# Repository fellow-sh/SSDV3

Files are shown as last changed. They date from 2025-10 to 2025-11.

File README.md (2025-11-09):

<p style="text-align: center;font-weight: bold;">This project has been migrated to the UBCO Aerospace Club <a href="https://github.com/UBCOAerospaceClub/2025_SSDV3">2025_SSDV3</a> fork.</p>

# The Super Step Down V3

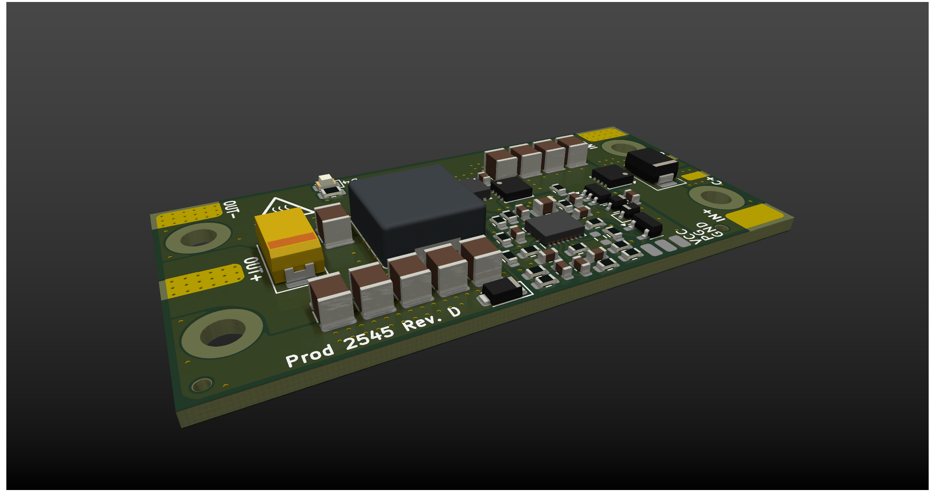
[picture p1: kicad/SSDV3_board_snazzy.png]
Top View


The SSDV3 is an independently-made, non-isolated DC/DC converter designed for unmanned aerial systems (UAS). The module is intended for converting 50V battery input down to 5-12V output at a maximum load of 8A. It acts as a reliable battery-eliminator circuit (BEC) through effective regulation in the presence of voltage transients caused by high-power brushless motors.

## Specifications

<table><tbody>
  <tr>
    <td>Input Voltage</td>
    <td>20-60V</td>
  </tr>
  <tr>
    <td>Max Transient Voltage</td>
    <td>100V (clamping starts at 70V)</td>
  </tr>
  <tr>
    <td>Output Voltage(s)</td>
    <td>5.1V, 7.4V, 9.6V, 12V</td>
  </tr>
  <tr>
    <td>Thermal Max Output Current</td>
    <td>5A</td>
  </tr>
  <tr>
    <td>Designed Max Output Current</td>
    <td>8A</td>
  </tr>
  <tr>
    <td>Lowest Typical Efficiency</td>
    <td>89%</td>
  </tr>
  <tr>
    <td>Est. Voltage Overshoot</td>
    <td>200mV</td>
  </tr>
</tbody>
</table>

*Specifications are from design, not tested.*

## Comparison with Last Super Step Down

This design is motivated by the challenges encountered by the [UBCO Aerospace Club](https://github.com/UBCOAerospaceClub) with their Jellyfish quadcopter when powering auxiliary electronics off the drone's main battery. Lessons were learned through a variety of integration failures, investigations, and validation testing, and these experiences informed the development of version 3 of the Super Step Down series.

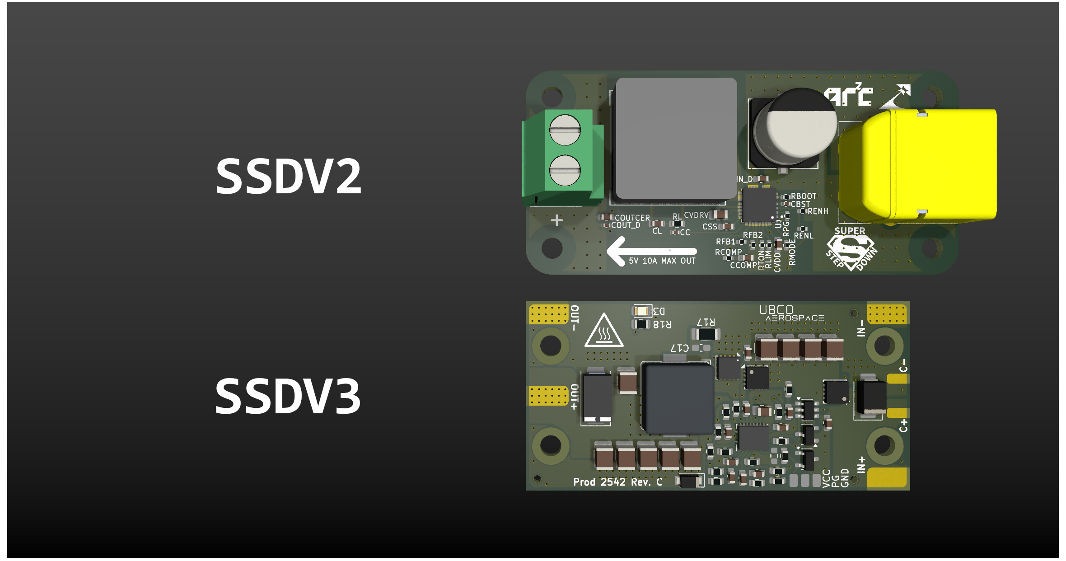
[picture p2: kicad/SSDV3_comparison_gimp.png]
Comparison


**Improvements from the previous version:**

- Dramatically improved regulation during line transients
- Considerable footprint area reduction by 16.5%
- Configurable output voltages instead of a fixed 5V output
- Added ESD protection on inputs
- Reverse polarity protection for the majority of the circuit
- Lower losses by using direct wire solder pads instead of terminal block

## Copyright Notice

Copyright &#169; Julian Joaquin 2025

Hardware Source Licensed under CERN-OHL-W version 2

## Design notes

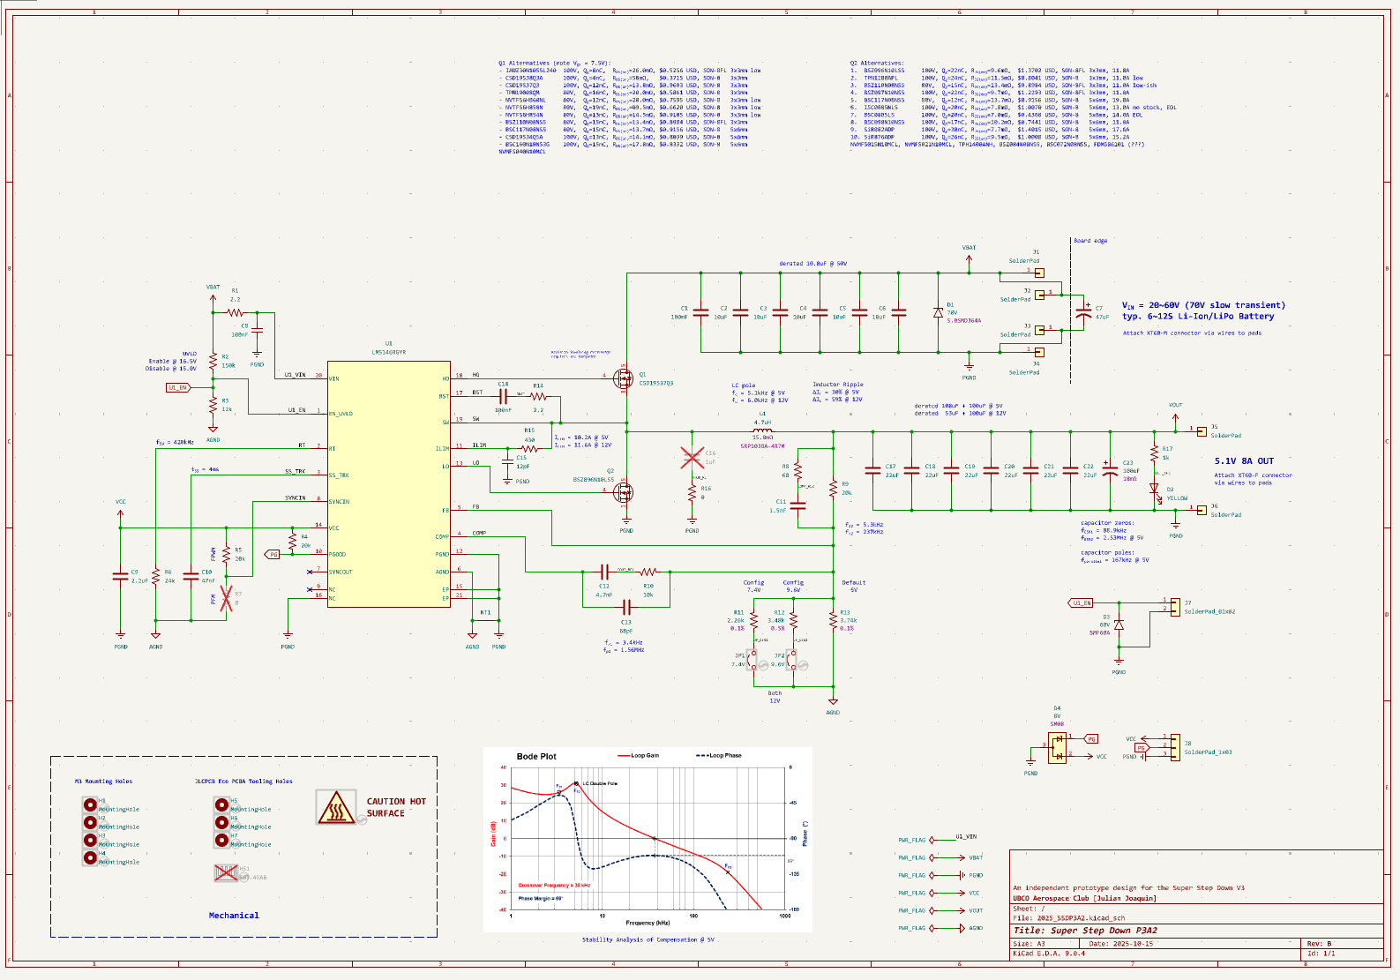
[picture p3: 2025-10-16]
kicad/SSDV3_schematic.png

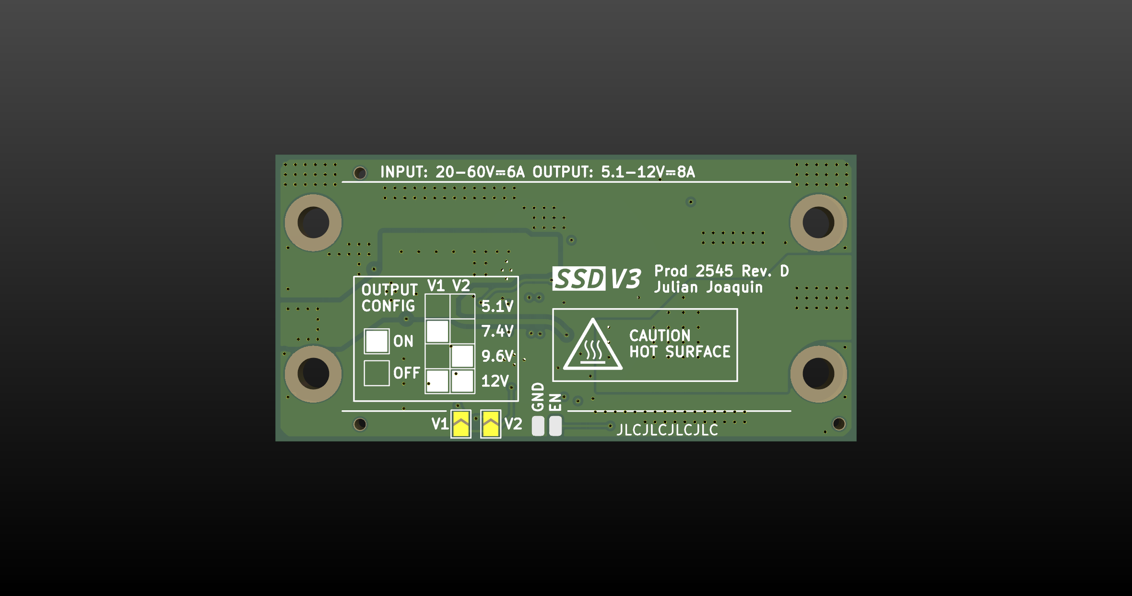
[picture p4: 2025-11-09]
kicad/SSDV3_board_bottom.png

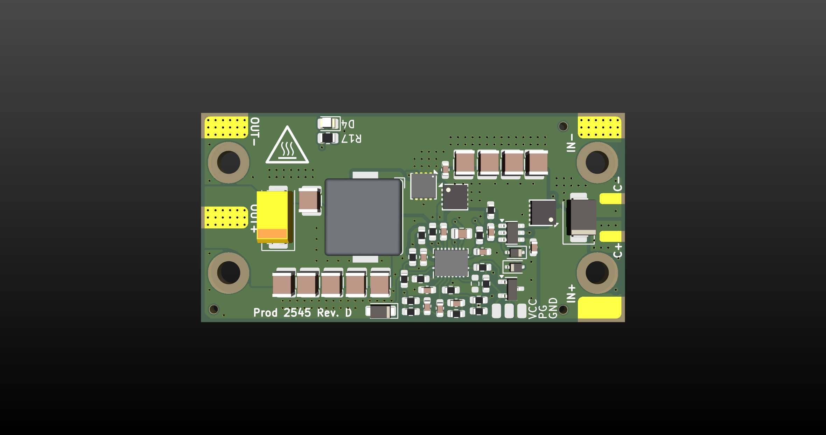
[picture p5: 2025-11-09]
kicad/SSDV3_board_top.png

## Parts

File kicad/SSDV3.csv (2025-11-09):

Value | Reference | Footprint | Datasheet | Part Number | Description | LCSC PN | Part Type | Manufacturer
2.2uF | C10 | Capacitor_SMD:C_0805_2012Metric | ~ | GRM21BR71E225KE11L | CAP CER 2.2uF 25V X7R 10% 0805 | C77081 | Extended | Murata Electronics
47nF | C11 | Capacitor_SMD:C_0603_1608Metric | ~ | CL10B473KB8NNNC | CAP CER 47nF 50V X7R 10% 0603 | C1622 | Basic | Panasonic
1.5nF | C12 | Capacitor_SMD:C_0603_1608Metric | ~ | 0603B152K500NT | CAP CER 1.5nF 50V X7R 10% 0603 | C1595 | Preferred Extended | Guangdong Fenghua
4.7nF | C13 | Capacitor_SMD:C_0603_1608Metric | ~ | 0603B472K500NT | CAP CER 4.7nF 50V X7R 10% 0603 | C53987 | Basic | Guangdong Fenghua
68pF | C14 | Capacitor_SMD:C_0603_1608Metric | ~ | CL10C680JB8NNNC | CAP CER 68pF 50V C0G 5% 0603 | C28262 | Preferred Extended | Panasonic
12pF | C16 | Capacitor_SMD:C_0603_1608Metric | ~ | CC0603JRNPO0BN120 | CAP CER 12pF 100V NP0 5% 0603 | C576801 | Extended | YAGEO
100uF | C23 | Capacitor_Tantalum_SMD:CP_EIA-7343-20_Kemet-V_HandSolder | https://search.kemet.com/download/specsheet/T521D107M025ATE040 | T521D107M025ATE040 | CAP TANT 100uF 25V 20% 7343 | C696814 | Extended | KEMET
22uF | C17,C18,C19,C20,C21,C22 | Capacitor_SMD:C_1210_3225Metric | https://product.samsungsem.com/mlcc/CL32B226KAJNNN.do | CL32B226KAJNNNE | CAP CER 22uF 25V X7R 10% 1210 | C309062 | Extended | Panasonic
100nF | C2,C3,C4,C9,C15 | Capacitor_SMD:C_0603_1608Metric | https://www.yageogroup.com/products/Capacitors/part/CC0603KRX7R0BB104 | CC0603KRX7R0BB104 | CAP CER 100nF 100V X7R 10% 0603 | C113803 | Extended | YAGEO
10uF | C5,C6,C7,C8 | Capacitor_SMD:C_1210_3225Metric | ~ | GRM32EC72A106KE05L | CAP CER 10uF 100V X7S 10% 1210 | C576517 | Extended | Murata Electronics
64V | D1 | Diode_SMD:D_SMB | https://jlcpcb.com/api/file/downloadByFileSystemAccessId/8564879160893476864 | SMBJ64CA | DIODE TVS 64V 600W BI SMB | C41376099 | Preferred Extended | Zhuhai Hongjiacheng
GREEN | D4 | LED_SMD:LED_0805_2012Metric | ~ | KT-0805G | LED GREEN 0805 | C2297 | Basic | Hubei KENTO Electronics
60V | D5 | Diode_SMD:D_SMF | https://jlcpcb.com/api/file/downloadByFileSystemAccessId/8564881124892696576 | SMF60CA | DIODE TVS 60V BI SOD-123FL | C41376092 | Preferred Extended | Zhuhai Hongjiacheng
8V | D6 | Package_TO_SOT_SMD:SOT-23-3 | https://jlcpcb.com/api/file/downloadByFileSystemAccessId/8604441956051673088 | SM08 | DIODE TVS DUAL 8V UNI SOT-23 | C42413902 | Preferred Extended | Zhuhai Hongjiacheng
BAT46WS | D2,D3 | Diode_SMD:D_SOD-323 | ~ | BAT46WS | DIODE SCHOTTKY 100V SOD-323 | C7502692 | Preferred Extended | Zhuhai Hongjiacheng
4.7uH | L1 | Inductor_SMD:L_Bourns_SRP1038C_10.0x10.0mm | https://www.bourns.com/docs/Product-Datasheets/SRP1038A.pdf | SRP1038A-4R7M | INDUCTOR 4.7uH 10A 15mΩ | C2041319 | Extended | Bourns
BSZ096N10LS5 | Q3 | Package_SON_JJ:Infineon_PG-TSDSON-8-26_3.3x3.3mm_P0.65mm | https://www.infineon.com/part/BSZ096N10LS5 | BSZ096N10LS5 | MOSFET N-CH 100V 62A TSDSON-8FL | C534695 | Extended | Infineon Technologies
CSD19537Q3 | Q1,Q2 | Package_SON_JJ:Texas_DQG0008A_3.3x3.3mm_P0.65mm_ThermalVias-D0.3mm | http://www.ti.com/lit/ds/symlink/csd19537q3.pdf | CSD19537Q3T | MOSFET N-CH 100V 53A VSON-8(3.3x3.3) | C134143 | Extended | Texas Instruments
150k | R3 | Resistor_SMD:R_0603_1608Metric | ~ | 0603WAF1503T5E | RES 150kΩ 1% 75V 100mW 0603 | C22807 | Basic | UNI-ROYAL
12k | R4 | Resistor_SMD:R_0603_1608Metric | ~ | 0603WAF1202T5E | RES 12kΩ 1% 75V 100mW 0603 | C22790 | Basic | UNI-ROYAL
24k | R7 | Resistor_SMD:R_0603_1608Metric | ~ | 0603WAF2402T5E | RES 24kΩ 1% 75V 100mW 0603 | C23352 | Basic | UNI-ROYAL
10k | R11 | Resistor_SMD:R_0603_1608Metric | ~ | 0603WAF1002T5E | RES 10kΩ 1% 75V 100mW 0603 | C25804 | Basic | UNI-ROYAL
6.81k | R12 | Resistor_SMD:R_0603_1608Metric | ~ | RT0603BRD076K81L | RES 6.81kΩ 0.1% 50V 100mW 0603 | C861538 | Extended | YAGEO
3.48k | R13 | Resistor_SMD:R_0603_1608Metric | ~ | 0603WAD3481T5E | RES 3.48kΩ 0.5% 50V 100mW 0603 | C423043 | Extended | UNI-ROYAL
3.74k | R14 | Resistor_SMD:R_0603_1608Metric | https://www.yageogroup.com/products/Resistors/part/RT0603BRE073K74L | RT0603BRE073K74L | RES 3.74kΩ 0.1% 75V 100mW 0603 | C849741 | Extended | YAGEO
430 | R16 | Resistor_SMD:R_0603_1608Metric | ~ | 0603WAF4300T5E | RES 430Ω 1% 75V 100mW 0603 | C23170 | Preferred Extended | UNI-ROYAL
1k | R17 | Resistor_SMD:R_0805_2012Metric | ~ | 0805W8F1001T5E | RES 1kΩ 1% 150V 125mW 0805 | C17513 | Basic | UNI-ROYAL
68 | R1,R9 | Resistor_SMD:R_0603_1608Metric | ~ | 0603WAF680JT5E | RES 68Ω 1% 75V 100mW 0603 | C27592 | Preferred Extended | UNI-ROYAL
2.2 | R2,R15 | Resistor_SMD:R_0603_1608Metric | ~ | 0603WAF220KT5E | RES 2.2Ω 1% 75V 100mW 0603 | C22939 | Basic | UNI-ROYAL
20k | R5,R6,R10 | Resistor_SMD:R_0603_1608Metric | ~ | 0603WAF2002T5E | RES 20kΩ 1% 75V 100mW 0603 | C4184 | Basic | UNI-ROYAL
LM5050-1 | U1 | Package_TO_SOT_SMD:TSOT-23-6 | http://www.ti.com/lit/ds/symlink/lm5050-1-q1.pdf | LM5050-1 | IC HIGH SIDE FET controller TSOT-23-6 | C473393 | Extended | Texas Instruments
LM5146 | U2 | Package_QFN_JJ:Texas_RGY0020B_EP_3.5x4.5mm_P0.5mm_ThermalVias-D0.3mm | https://www.ti.com/lit/gpn/lm5146 | LM5146RGYR | IC BUCK SYNC Controller VQFN-20 | C3188679 | Extended | Texas Instruments

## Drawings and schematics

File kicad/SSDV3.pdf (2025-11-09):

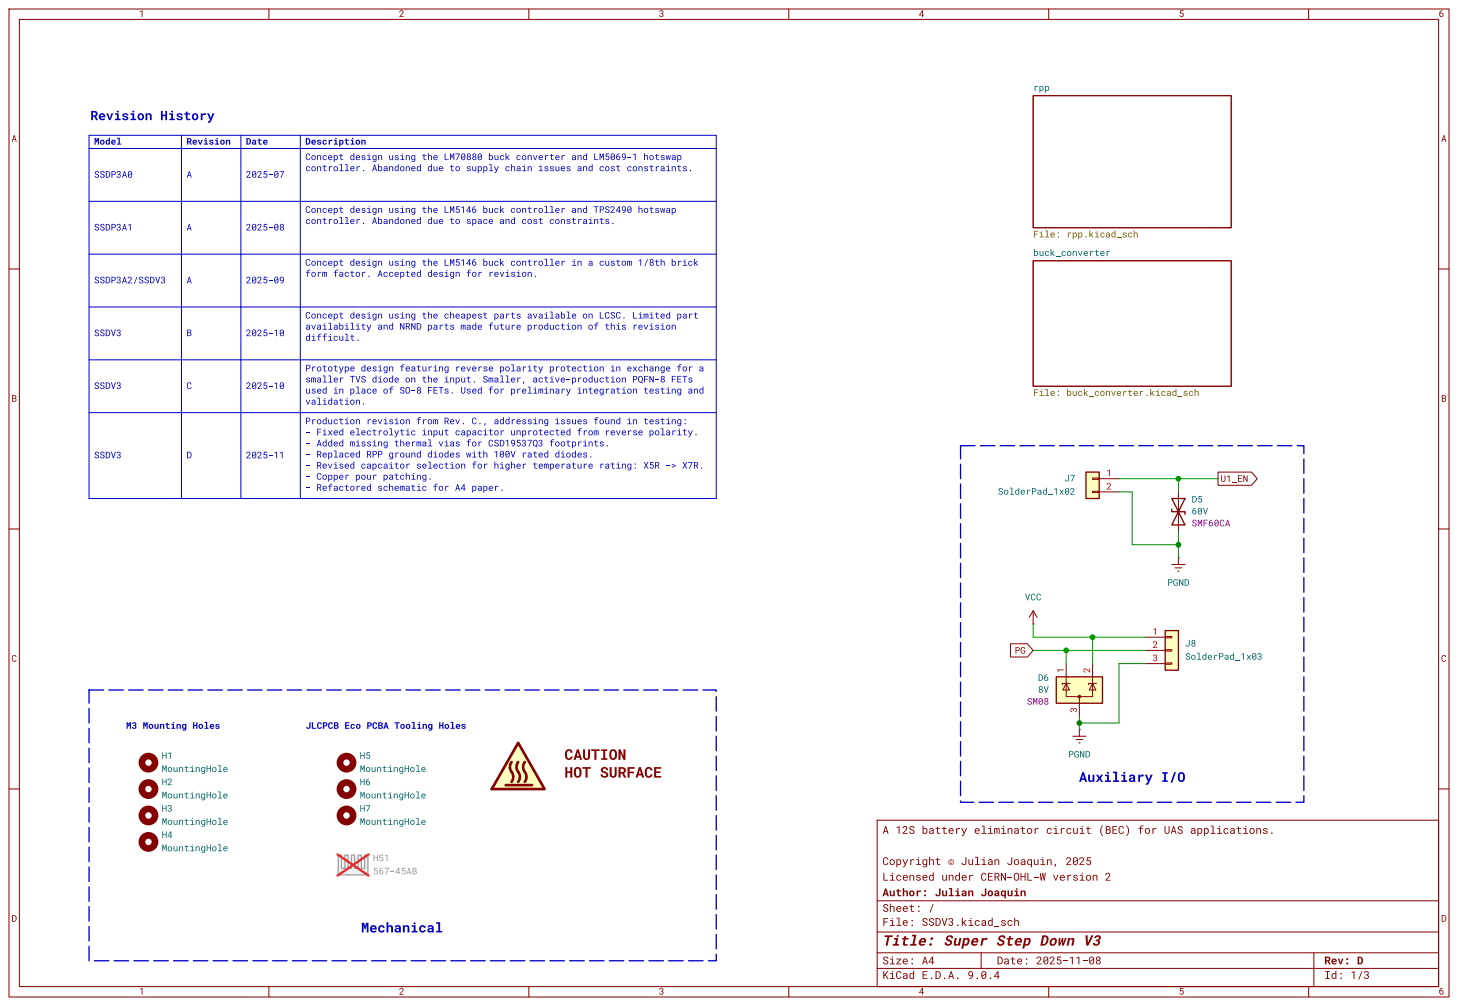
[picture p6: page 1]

Revision A C | Date 2025-07 2025-10 | Description SSDP3A0 Concept design using the LM70880 buck converter and LM5069-1 hotswap difficult. SSDV3 Prototype design featuring reverse polarity protection in exchange for a | PG Model

A | 2025-08 | controller. Concept design using the LM5146 buck controller Abandoned due to supply chain issues and cost constraints. SSDP3A1 and TPS2490 hotswap

A | 2025-09 | controller. Concept design using the LM5146 buck controller Abandoned due to space and cost constraints. SSDP3A2/SSDV3 in a custom 1/8th brick

B | 2025-10 | form factor. Concept design using the cheapest parts available Accepted design for revision. SSDV3 and NRNDparts made future production on LCSC. Limited of this revision part availability

smaller TVS diode on the input. Smaller, active-production integration PQFN-8 FETs used in place of SO-8 FETs. Used for preliminary testing and

JLCPCB Eco PCBA Tooling Holes

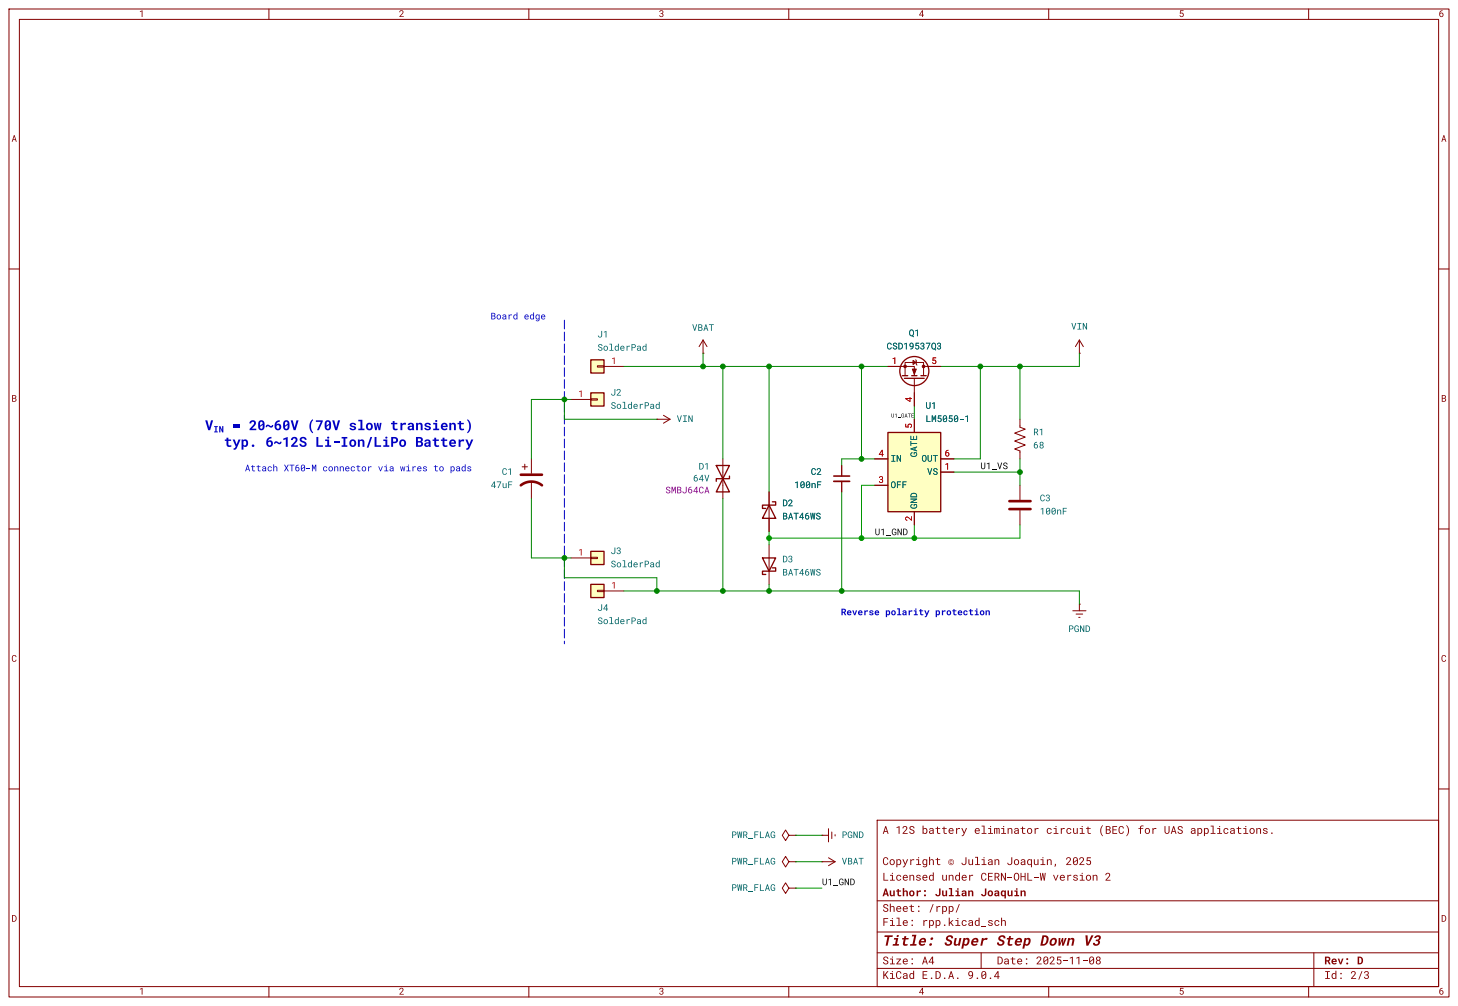
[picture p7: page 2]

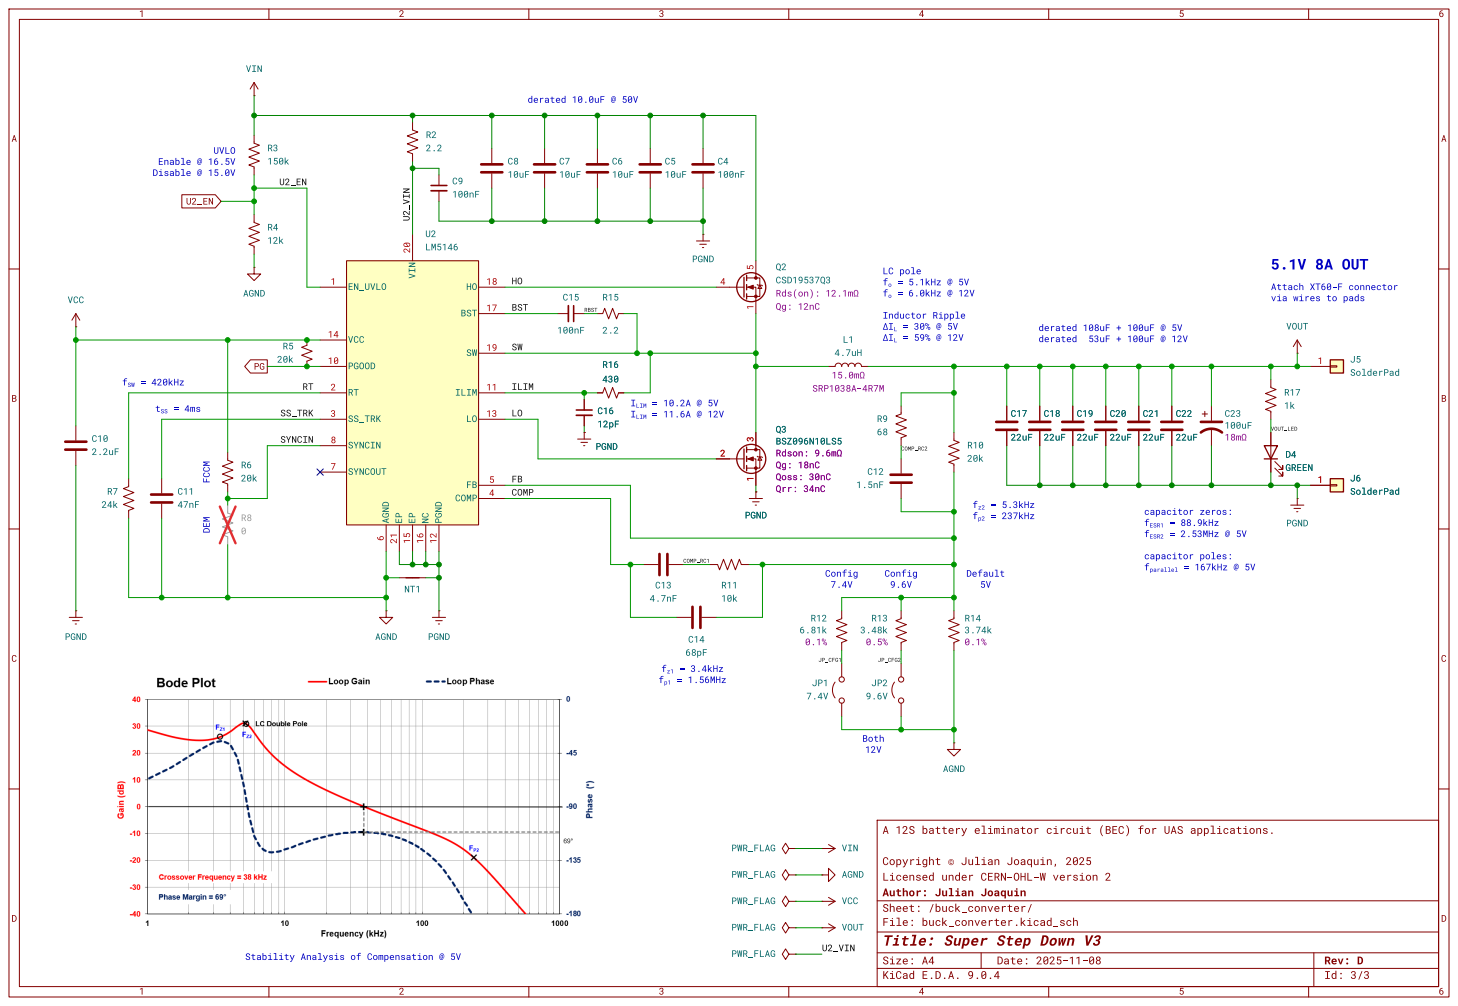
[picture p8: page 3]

6 EP 21 VIN 20 EP 15 NC 16 PGND 12 HO

Attach XT60-F connector via wires to pads

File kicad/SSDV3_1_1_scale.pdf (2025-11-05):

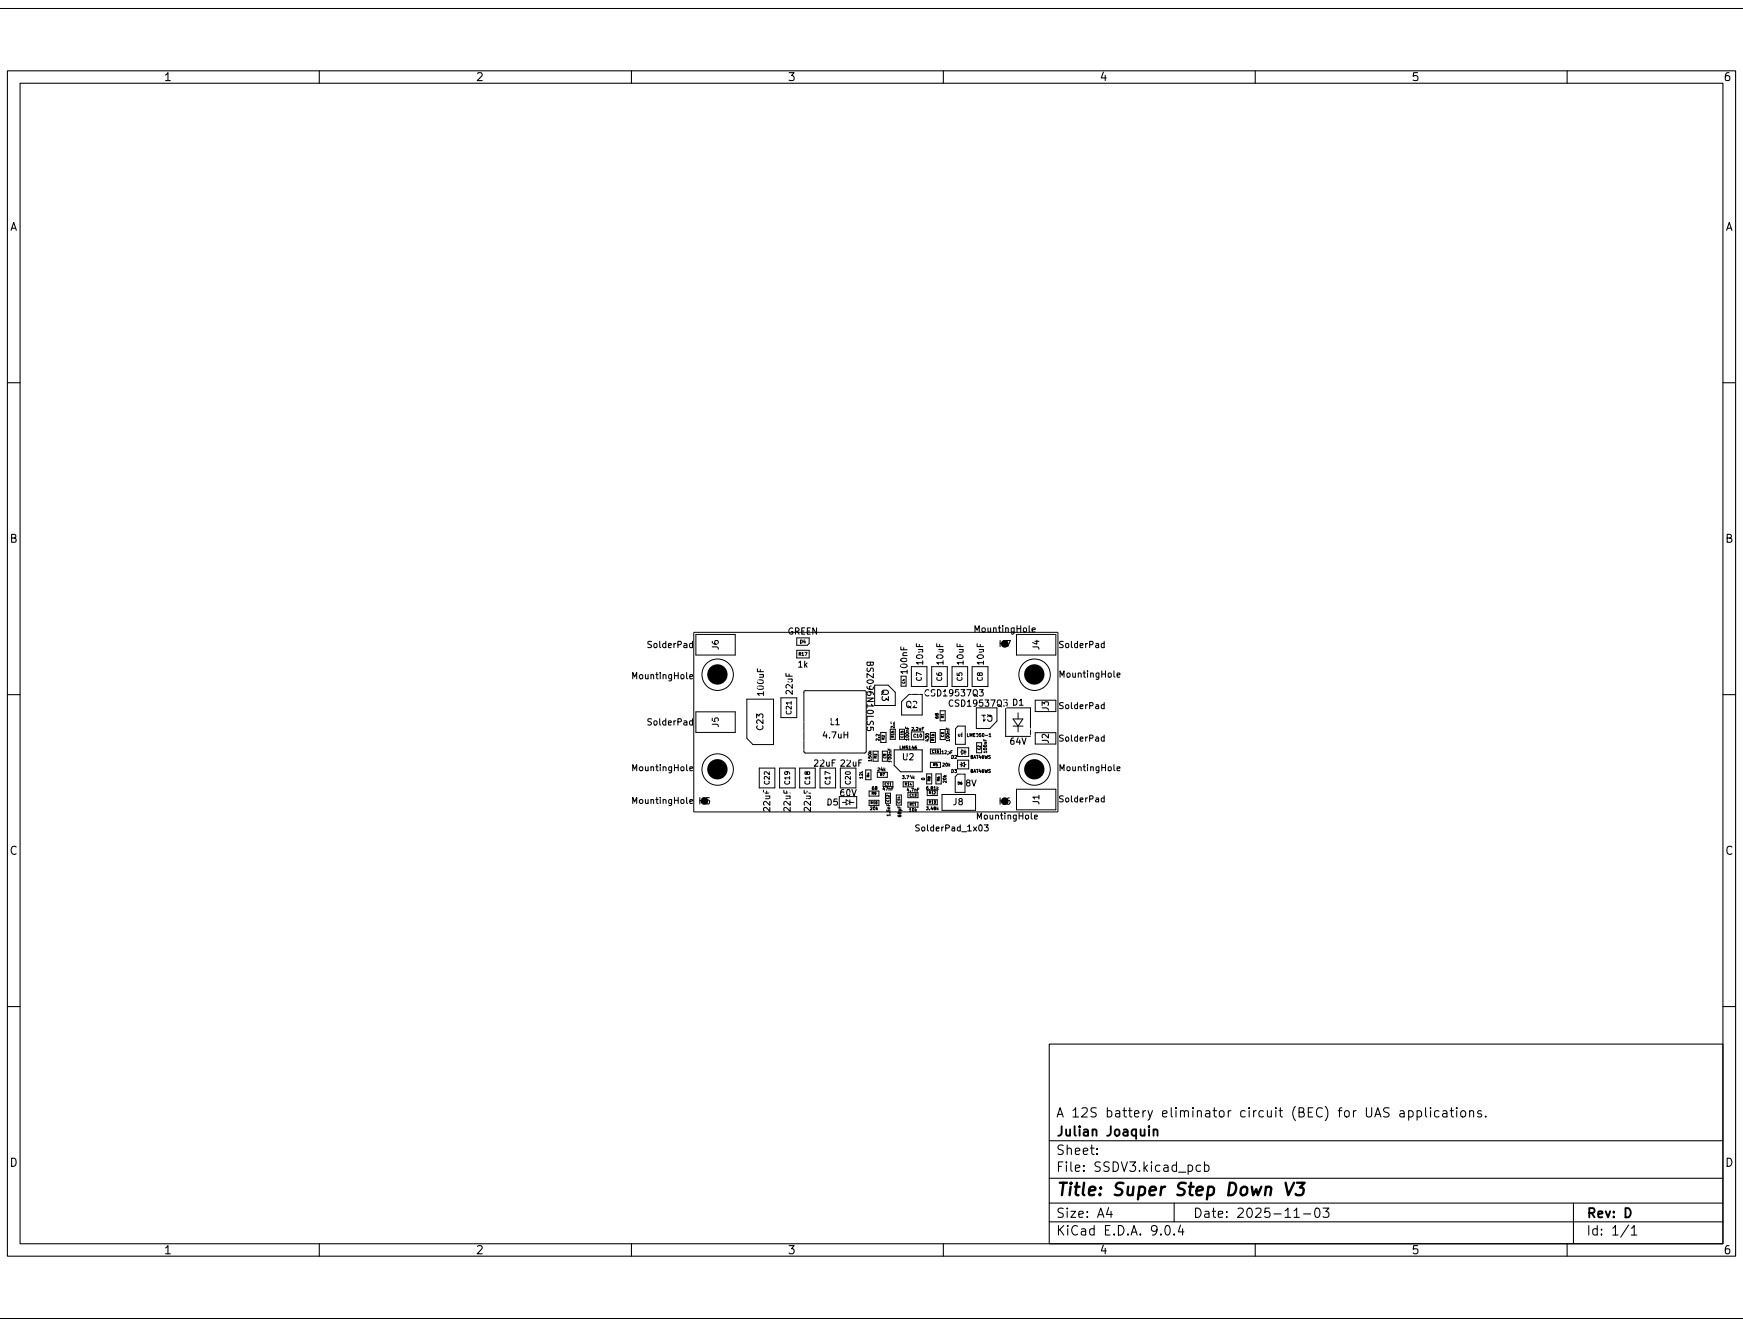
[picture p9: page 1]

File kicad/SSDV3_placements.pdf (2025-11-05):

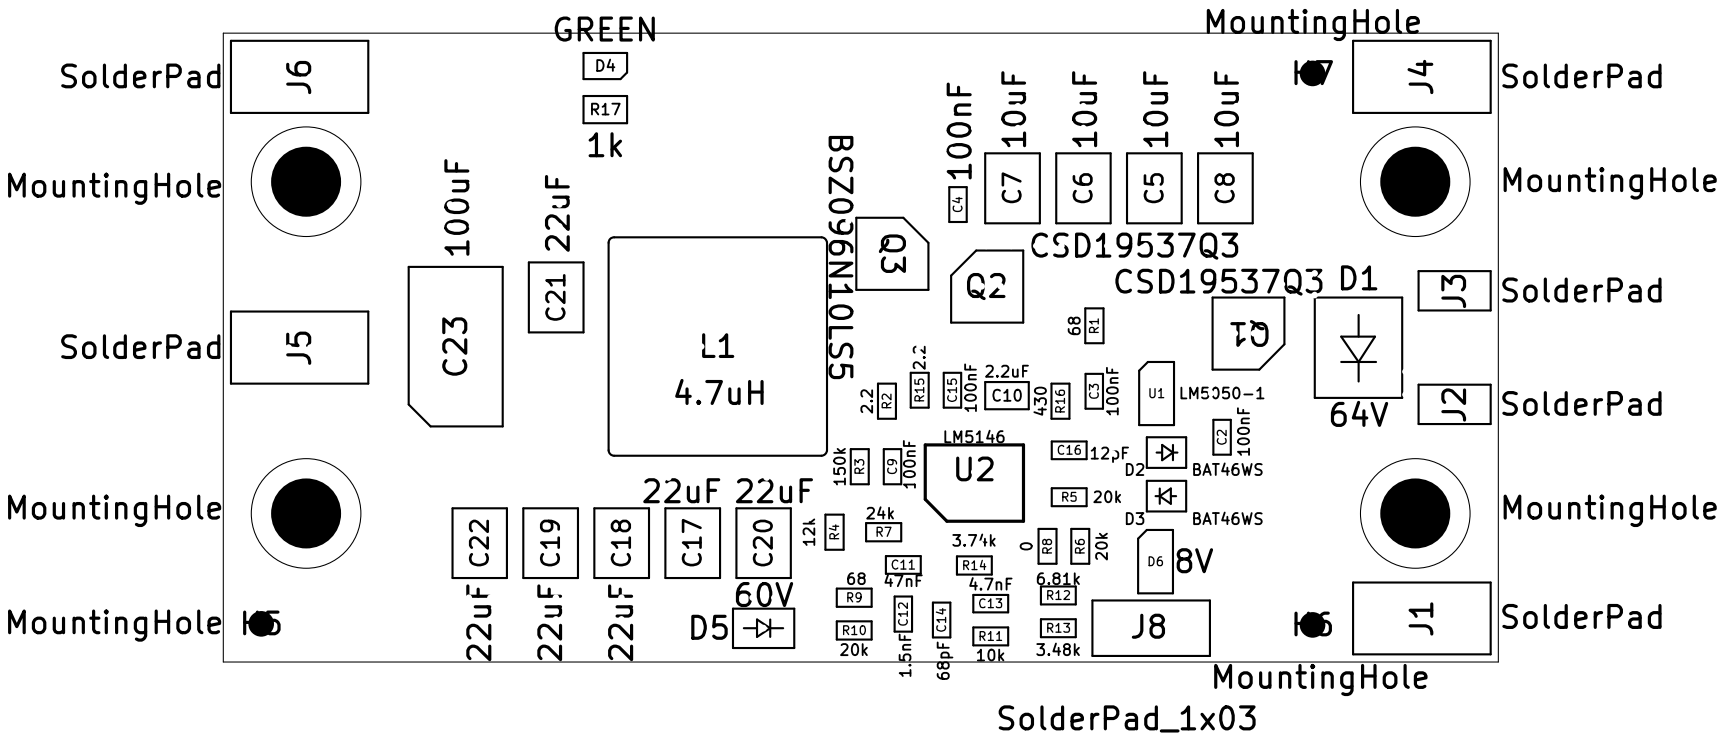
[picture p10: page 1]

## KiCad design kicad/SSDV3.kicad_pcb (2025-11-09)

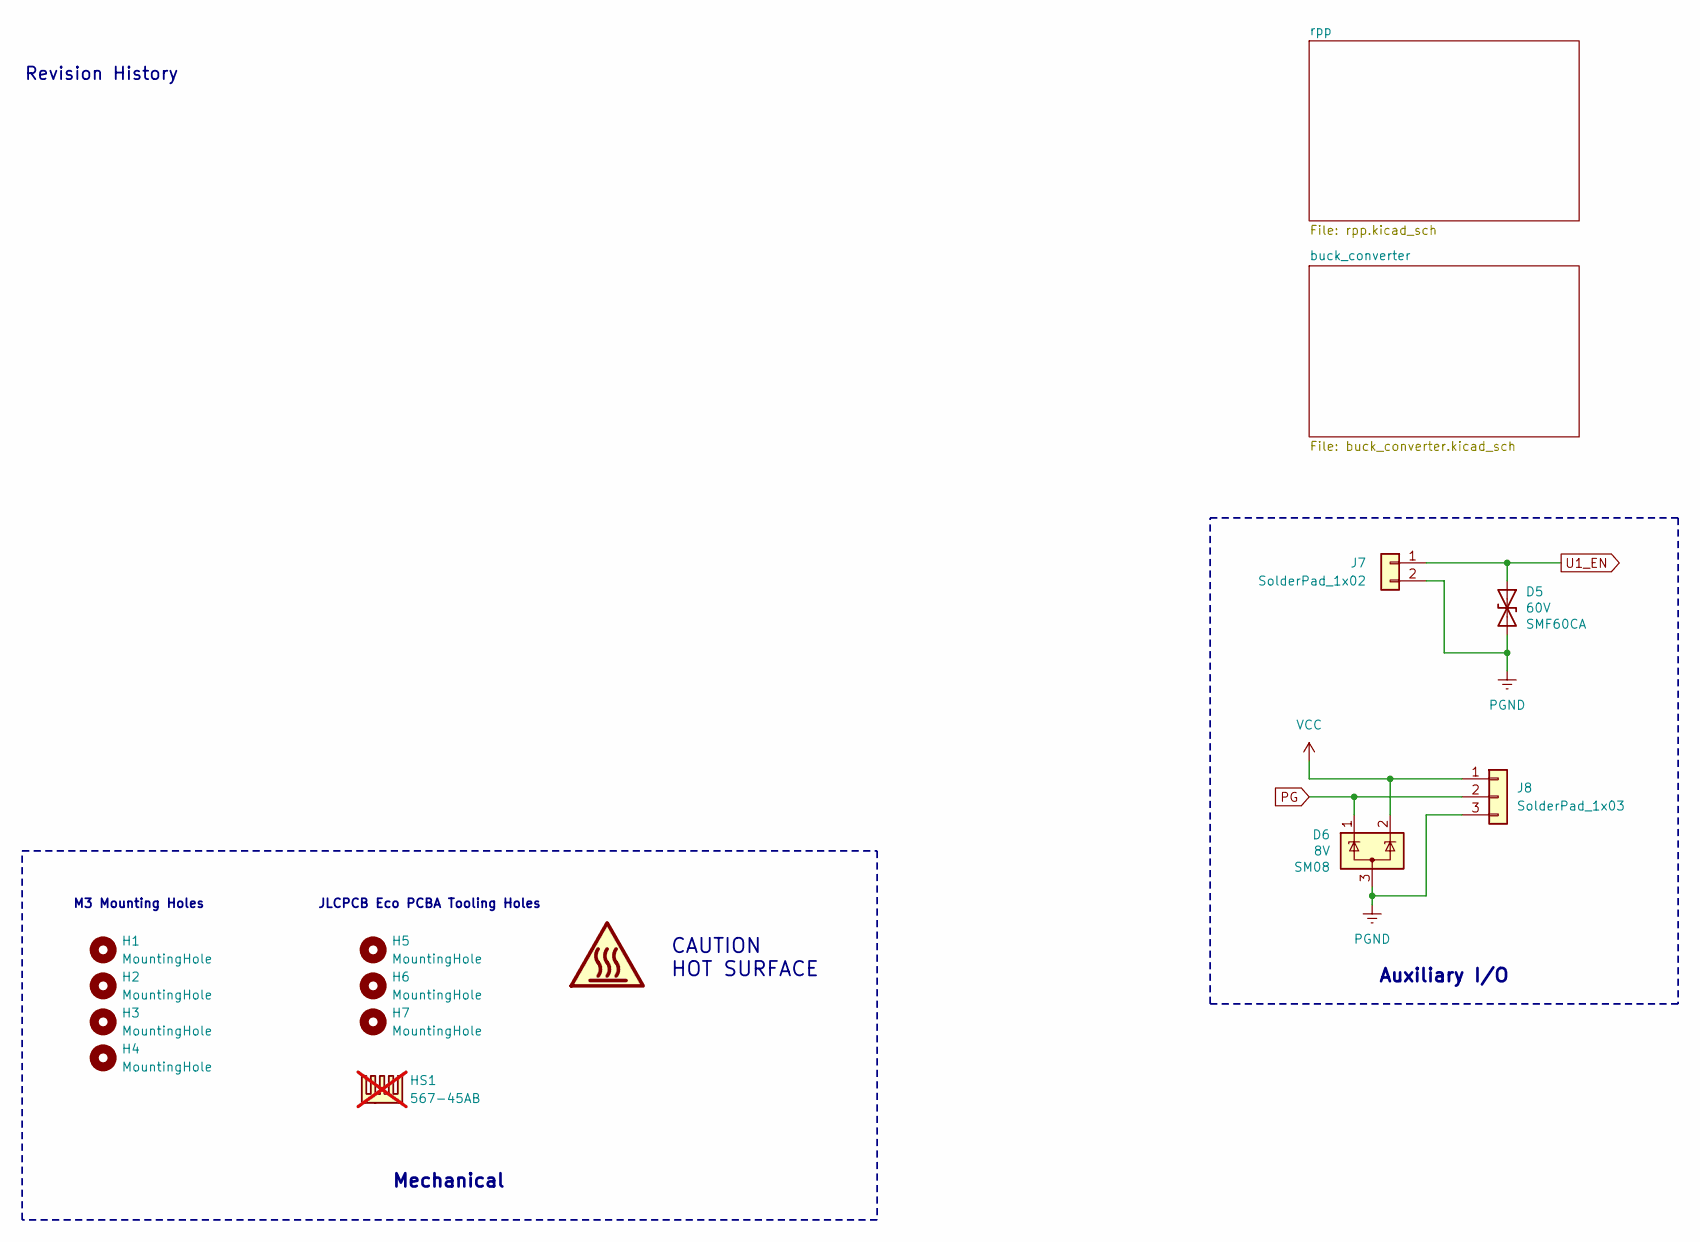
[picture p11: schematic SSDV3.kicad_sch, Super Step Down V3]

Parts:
D5: 60V; D_SMF; Voltage 60V; Part Number SMF60CA; LCSC PN C41376092
D6: 8V; SOT-23-3; Voltage 8V; Part Number SM08; LCSC PN C42413902
H1, H2, H3, H4: MountingHole; MountingHole_3.2mm_M3_ISO7380
H5, H6, H7: MountingHole; ToolingHole_1.152mm
HS1: 567-45AB; not fitted
J7: SolderPad_1x02; SolderWirePad_1x02_SMD_1.5x2mm
J8: SolderPad_1x03; SolderWirePad_1x03_SMD_1.5x2mm

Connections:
PG: D6.1 (K), J8.2; also elsewhere on the board
PGND: D5.2 (A2), D6.3 (A), J7.2, J8.3; also elsewhere on the board
VCC: D6.2 (K), J8.1; also elsewhere on the board

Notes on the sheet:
M3 Mounting Holes
Auxiliary I/O
CAUTION HOT SURFACE
Revision History
JLCPCB Eco PCBA Tooling Holes
Mechanical

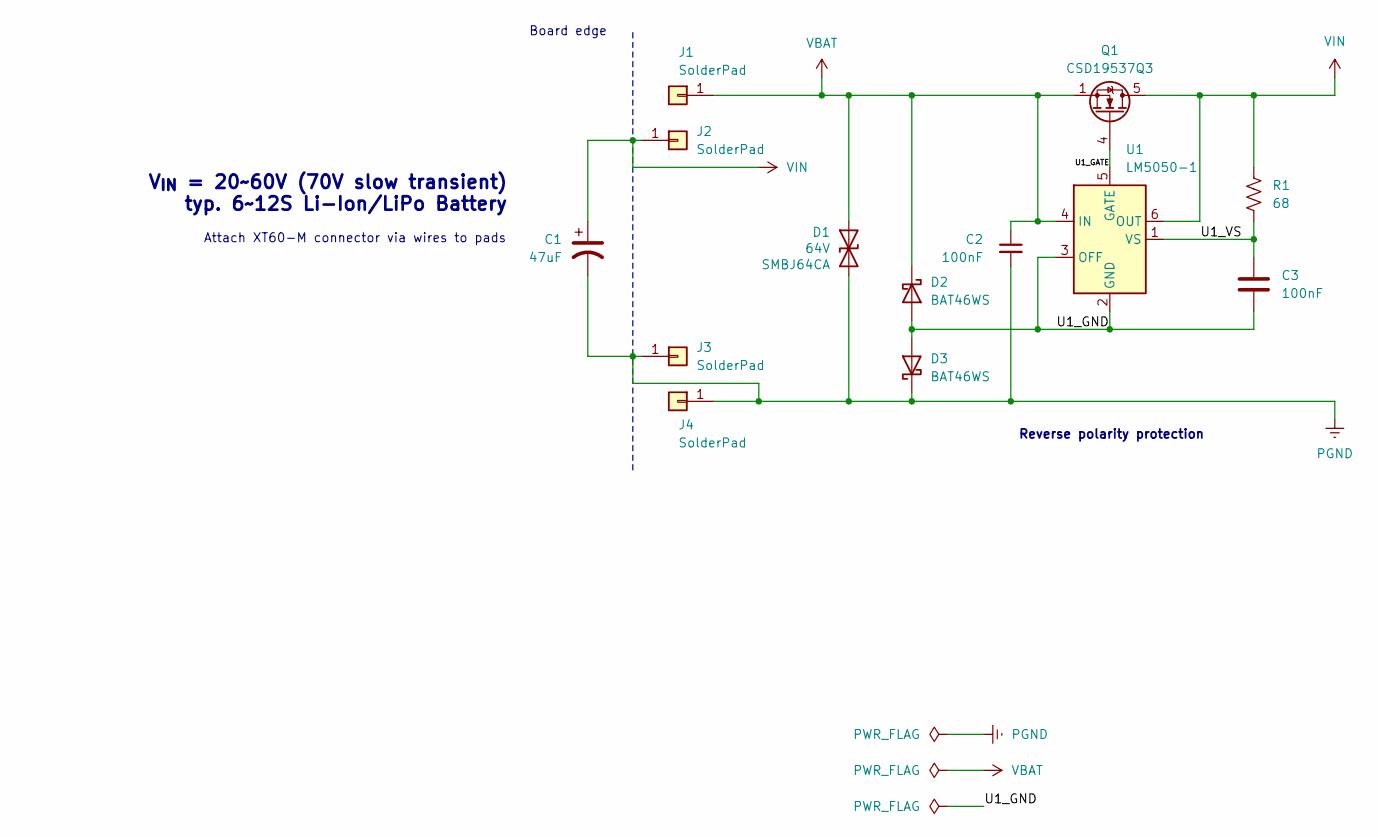
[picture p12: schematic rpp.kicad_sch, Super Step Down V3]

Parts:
C1: 47uF; Part Number ESH476M100AH9AA; LCSC PN C5113349
C2, C3: 100nF; C_0603_1608Metric; Voltage 100V; Tolerance 10%; Part Type Extended; LCSC PN C113803
D1: 64V; D_SMB; Voltage 103V; Part Number SMBJ64CA; LCSC PN C41376099
D2, D3: BAT46WS; D_SOD-323; Part Number BAT46WS; LCSC PN C7502692
J1, J4: SolderPad; SolderWirePad_1x01_SMD_3x6mm
J2, J3: SolderPad; SolderWirePad_1x01_SMD_1.5x3mm
Q1: CSD19537Q3; Texas_DQG0008A_3.3x3.3mm_P0.65mm_ThermalVias-D0.3mm; Part Number CSD19537Q3T; LCSC PN C134143
R1: 68; R_0603_1608Metric; Voltage 75V; Tolerance 1%; Part Type Preferred Extended; LCSC PN C27592
U1: LM5050-1; TSOT-23-6; Part Number LM5050-1; LCSC PN C473393

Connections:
/rpp/U1_GATE: Q1.4 (G), U1.5 (GATE)
/rpp/U1_GND: C3.2, D2.2 (A), D3.2 (A), U1.2 (GND), U1.3 (OFF)
/rpp/U1_VS: C3.1, R1.2, U1.1 (VS)
PGND: C1.2, C2.2, D1.2 (A2), D3.1 (K), J3.1, J4.1; also elsewhere on the board
VBAT: C2.1, D1.1 (A1), D2.1 (K), J1.1, Q1.1 (S), Q1.2 (S), Q1.3 (S), U1.4 (IN)
VIN: C1.1, J2.1, Q1.5 (D), R1.1, U1.6 (OUT); also elsewhere on the board

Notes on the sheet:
Reverse polarity protection
Board edge
V_{IN} = 20~60V (70V slow transient) typ. 6~12S Li-Ion/LiPo Battery
Attach XT60-M connector via wires to pads

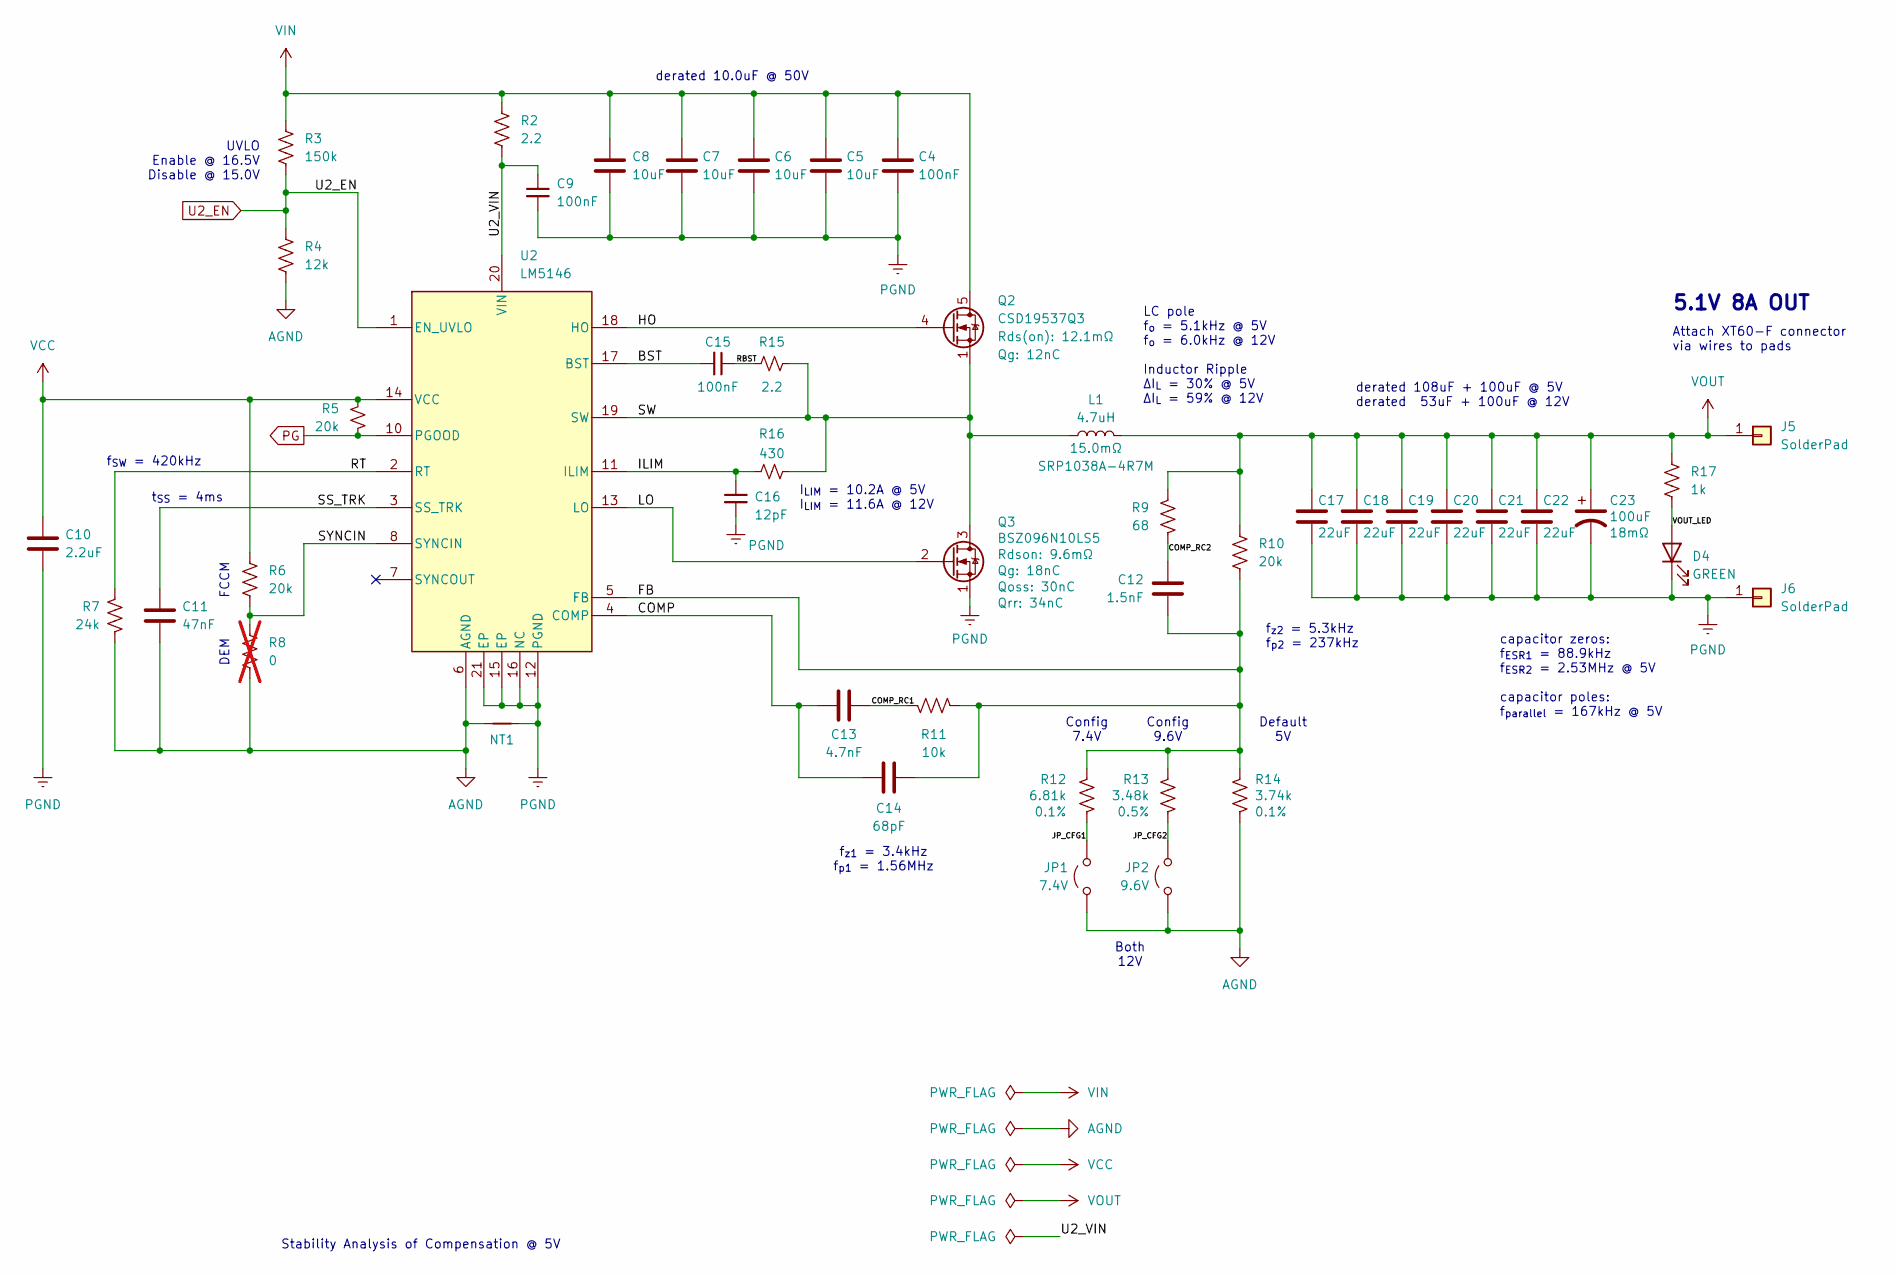
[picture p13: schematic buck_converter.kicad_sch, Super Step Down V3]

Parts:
C4, C9, C15: 100nF; C_0603_1608Metric; Voltage 100V; Tolerance 10%; Part Type Extended; LCSC PN C113803
C5, C6, C7, C8: 10uF; C_1210_3225Metric; Voltage 100V; Tolerance 10%; Part Type Extended; LCSC PN C576517
C10: 2.2uF; C_0805_2012Metric; Voltage 25V; Tolerance 10%; Part Type Extended; LCSC PN C77081
C11: 47nF; C_0603_1608Metric; Voltage 50V; Tolerance 10%; Part Type Basic; LCSC PN C1622
C12: 1.5nF; C_0603_1608Metric; Voltage 50V; Tolerance 10%; Part Type Preferred Extended; LCSC PN C1595
C13: 4.7nF; C_0603_1608Metric; Voltage 50V; Tolerance 10%; Part Type Basic; LCSC PN C53987
C14: 68pF; C_0603_1608Metric; Voltage 50V; Tolerance 5%; Part Type Preferred Extended; LCSC PN C28262
C16: 12pF; C_0603_1608Metric; Voltage 100V; Tolerance 5%; Part Type Extended; LCSC PN C576801
C17, C18, C19, C20, C21, C22: 22uF; C_1210_3225Metric; Voltage 25V; Tolerance 10%; Part Type Extended; LCSC PN C309062
C23: 100uF; CP_EIA-7343-20_Kemet-V_HandSolder; Tolerance 20%; Voltage 25V; Part Type Extended; LCSC PN C696814
D4: GREEN; LED_0805_2012Metric; Part Type Basic; LCSC PN C2297
J5, J6: SolderPad; SolderWirePad_1x01_SMD_3x6mm
JP1: 7.4V; SolderJumper-2_P1.3mm_Open_TrianglePad1.0x1.5mm
JP2: 9.6V; SolderJumper-2_P1.3mm_Open_TrianglePad1.0x1.5mm
L1: 4.7uH; L_Bourns_SRP1038C_10.0x10.0mm; Tolerance 20%; Part Number SRP1038A-4R7M; LCSC PN C2041319
NT1: NetTie_2; NetTie-2_SMD_Pad0.5mm
Q2: CSD19537Q3; Texas_DQG0008A_3.3x3.3mm_P0.65mm_ThermalVias-D0.3mm; Voltage 100V; Part Type Extended; LCSC PN C134143
Q3: BSZ096N10LS5; Infineon_PG-TSDSON-8-26_3.3x3.3mm_P0.65mm; Voltage 100V; Part Number BSZ096N10LS5; LCSC PN C534695
R2, R15: 2.2; R_0603_1608Metric; Voltage 75V; Tolerance 1%; Part Type Basic; LCSC PN C22939
R3: 150k; R_0603_1608Metric; Tolerance 1%; Voltage 75V; Part Type Basic; LCSC PN C22807
R4: 12k; R_0603_1608Metric; Tolerance 1%; Voltage 75V; Part Type Basic; LCSC PN C22790
R5, R6, R10: 20k; R_0603_1608Metric; Voltage 75V; Tolerance 1%; Part Type Basic; LCSC PN C4184
R7: 24k; R_0603_1608Metric; Voltage 75V; Tolerance 1%; Part Type Basic; LCSC PN C23352
R8: 0; R_0603_1608Metric; not fitted
R9: 68; R_0603_1608Metric; Voltage 75V; Tolerance 1%; Part Type Preferred Extended; LCSC PN C27592
R11: 10k; R_0603_1608Metric; Voltage 75V; Tolerance 1%; Part Type Basic; LCSC PN C25804
R12: 6.81k; R_0603_1608Metric; Voltage 50V; Tolerance 0.1%; Part Type Extended; LCSC PN C861538
R13: 3.48k; R_0603_1608Metric; Voltage 50V; Tolerance 0.5%; Part Type Extended; LCSC PN C423043
R14: 3.74k; R_0603_1608Metric; Tolerance 0.1%; Voltage 75V; Part Type Extended; LCSC PN C849741
R16: 430; R_0603_1608Metric; Voltage 75V; Tolerance 1%; Part Type Preferred Extended; LCSC PN C23170
R17: 1k; R_0805_2012Metric; Voltage 150V; Tolerance 1%; Part Type Basic; LCSC PN C17513
U2: LM5146; Texas_RGY0020B_EP_3.5x4.5mm_P0.5mm_ThermalVias-D0.3mm; Voltage 100V; Part Type Extended; LCSC PN C3188679

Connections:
/buck_converter/BST: C15.2, U2.17 (BST)
/buck_converter/COMP: C13.1, C14.2, U2.4 (COMP)
/buck_converter/COMP_RC1: C13.2, R11.2
/buck_converter/COMP_RC2: C12.1, R9.2
/buck_converter/FB: C12.2, C14.1, R10.2, R11.1, R12.1, R13.1, R14.1, U2.5 (FB)
/buck_converter/HO: Q2.4 (G), U2.18 (HO)
/buck_converter/ILIM: C16.1, R16.2, U2.11 (ILIM)
/buck_converter/JP_CFG1: JP1.2 (B), R12.2
/buck_converter/JP_CFG2: JP2.2 (B), R13.2
/buck_converter/LO: Q3.2 (G), U2.13 (LO)
/buck_converter/RBST: C15.1, R15.1
/buck_converter/RT: R7.1, U2.2 (RT)
/buck_converter/SS_TRK: C11.1, U2.3 (SS_TRK)
/buck_converter/SW: L1.1, Q2.1 (S), Q2.2 (S), Q2.3 (S), Q3.3 (D), R15.2, R16.1, U2.19 (SW)
/buck_converter/SYNCIN: R6.2, R8.1, U2.8 (SYNCIN)
/buck_converter/U2_VIN: C9.1, R2.2, U2.20 (VIN)
/buck_converter/VOUT_LED: D4.2 (A), R17.2
AGND: C11.2, JP1.1 (A), JP2.1 (A), NT1.2, R4.2, R7.2, R8.2, R14.2, U2.6 (AGND)
PG: R5.2, U2.10 (PGOOD); also elsewhere on the board
PGND: C4.2, C5.2, C6.2, C7.2, C8.2, C9.2, C10.2, C16.2, C17.2, C18.2, C19.2, C20.2, C21.2, C22.2, C23.2, D4.1 (K), J6.1, NT1.1, Q3.1 (S), U2.12 (PGND), U2.15 (EP), U2.16 (NC), U2.21 (EP); also elsewhere on the board
VCC: C10.1, R5.1, R6.1, U2.14 (VCC); also elsewhere on the board
VIN: C4.1, C5.1, C6.1, C7.1, C8.1, Q2.5 (D), R2.1, R3.1; also elsewhere on the board
VOUT: C17.1, C18.1, C19.1, C20.1, C21.1, C22.1, C23.1, J5.1, L1.2, R9.1, R10.1, R17.1

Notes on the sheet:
capacitor zeros: f_{ESR1} = 88.9kHz f_{ESR2} = 2.53MHz @ 5V capacitor poles: f_{parallel} = 167kHz @ 5V
f_{SW} = 420kHz
FCCM
t_{SS} = 4ms
Config 9.6V
Stability Analysis of Compensation @ 5V
DEM
Default 5V
5.1V 8A OUT
derated 10.0uF @ 50V
UVLO Enable @ 16.5V Disable @ 15.0V
Config 7.4V
Attach XT60-F connector via wires to pads
f_{z1} = 3.4kHz f_{p1} = 1.56MHz
f_{z2} = 5.3kHz f_{p2} = 237kHz
I_{LIM} = 10.2A @ 5V I_{LIM} = 11.6A @ 12V
Both 12V
LC pole f_{o} = 5.1kHz @ 5V f_{o} = 6.0kHz @ 12V Inductor Ripple ΔI_{L} = 30% @ 5V ΔI_{L} = 59% @ 12V
derated 108uF + 100uF @ 5V derated 53uF + 100uF @ 12V

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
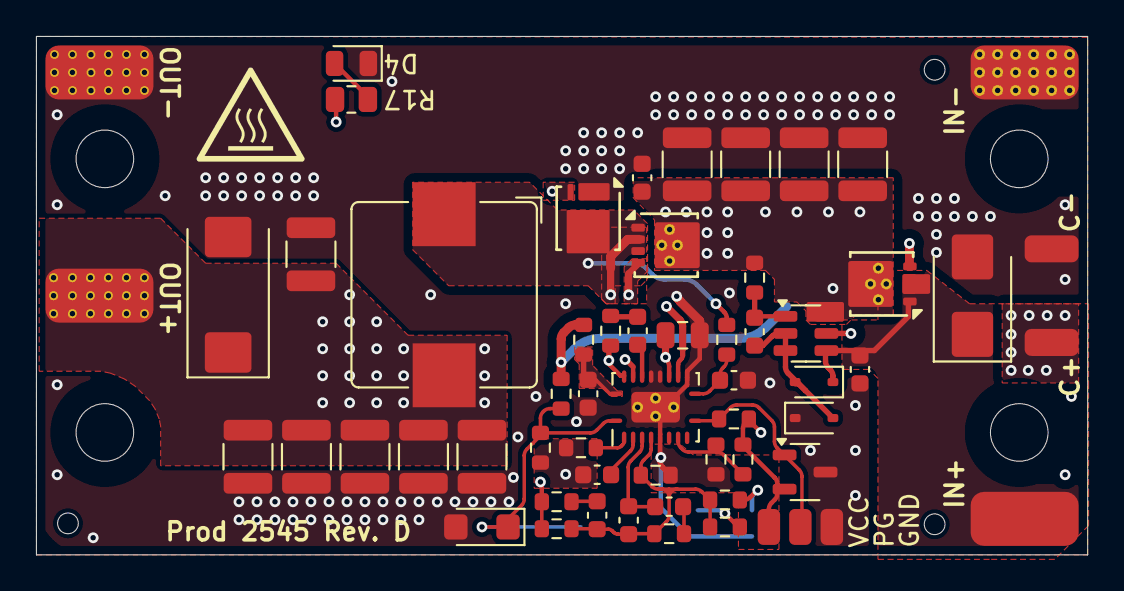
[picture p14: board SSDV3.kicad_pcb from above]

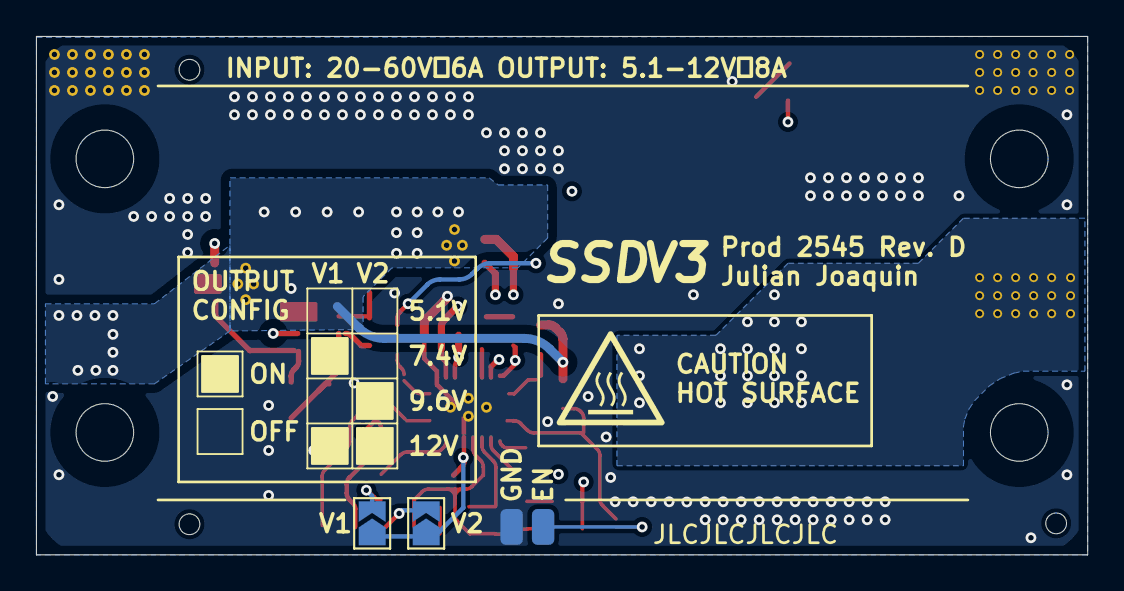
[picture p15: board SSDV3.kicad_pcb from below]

Board: 4 copper layers, 58.4 x 28.8 mm, 69 parts (3 on the bottom side), 28 nets.

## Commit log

2025-09-20 Revised PCB layout
    [2025_SSDP3A2.kicad_pcb, 2025_SSDP3A2.kicad_sch, 2025_SSDP3A2_iter3.csv]
2025-09-20 Note to change iLim
    [2025_SSDP3A2.kicad_sch]
2025-09-21 Revised MOSFET selection
    [2025_SSDP3A2.kicad_sch]
2025-09-22 Revised ILIM setting, added TVS
    [2025_SSDP3A2.kicad_pcb, 2025_SSDP3A2.kicad_sch]
2025-09-22 Revised PCB layout, simplified EMI filter
    [2025_SSDP3A2.kicad_pcb, 2025_SSDP3A2.kicad_sch, 2025_SSDP3A2_iter4.csv]
2025-09-22 Validated soft start circuit
2025-09-23 Updated ILIM values
    [2025_SSDP3A2.kicad_pcb, 2025_SSDP3A2.kicad_sch]
2025-09-24 Something changed
    [2025_SSDP3A2.kicad_pcb]
2025-09-25 Updated schematic
2025-09-26 Revised simulations, revised compensation network
    [2025_SSDP3A2.kicad_pcb, 2025_SSDP3A2.kicad_sch]
2025-09-29 Changed output capacitors for better layout
    [2025_SSDP3A2.kicad_pcb, 2025_SSDP3A2.kicad_sch]
2025-09-29 Corrected date
    [2025_SSDP3A2.kicad_pcb, 2025_SSDP3A2.kicad_sch]
2025-09-29 Began board routing, added README
    [2025_SSDP3A2.kicad_pcb]
2025-09-29 Revised output cap placement
    [2025_SSDP3A2.kicad_pcb]
2025-09-30 Removed soldermask around screw holes
    [2025_SSDP3A2.kicad_pcb]
2025-09-30 Revised mounting holes, bode plot, routing
    [2025_SSDP3A2.kicad_pcb, 2025_SSDP3A2.kicad_sch, 2025_SSDP3A2_iter1.csv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]
2025-09-30 Adjusted revision system
    [2025_SSDP3A2.kicad_pcb, 2025_SSDP3A2.kicad_sch]
2025-10-01 Using PQFN FETs instead of SuperSO-8
    [2025_SSDP3A2.kicad_pcb, 2025_SSDP3A2.kicad_sch]
2025-10-01 Finished routing
    [2025_SSDP3A2.kicad_pcb, 2025_SSDP3A2.kicad_sch]
2025-10-01 Added silkscreen markings, tweaked routing
    [2025_SSDP3A2.kicad_pcb]
2025-10-01 Tweaked routing, changed some fab parameters
    [2025_SSDP3A2.kicad_pcb, 2025_SSDP3A2.kicad_sch]
2025-10-03 Tweaked routing
    [2025_SSDP3A2.kicad_pcb]
2025-10-04 Tweaked feedback routing and removed EMI filter
    The EMI filter places an inductor in between the battery and the buck
    converter, creating the risk of resonance either at the buck converter
    input or on the battery line. While the former issue has been *somewhat*
    addressed with the parallel damping resistor, the latter issue cannot be
    reasonably fixed without good knowledge of the other various loads that
    may be attached to the battery line. For this reason, the EMI filter is
    removed.
    [2025_SSDP3A2.kicad_pcb, 2025_SSDP3A2.kicad_sch]
2025-10-04 Changed schematic and board pictures
2025-10-04 Tweaked routing layers
    [2025_SSDP3A2.kicad_pcb]
2025-10-05 Tweaked routing, added breakout pads, via clean up
    [2025_SSDP3A2.kicad_pcb, 2025_SSDP3A2.kicad_sch]
2025-10-05 Added 7.4V output support
    [2025_SSDP3A2.kicad_pcb, 2025_SSDP3A2.kicad_sch]
2025-10-05 Final tweaks
    [2025_SSDP3A2.kicad_pcb, 2025_SSDP3A2.kicad_sch]
2025-10-06 Added more capacitors to meet overshoot requirements
    [2025_SSDP3A2.kicad_pcb, 2025_SSDP3A2.kicad_sch]
2025-10-06 Tweaks in schematic and layout
    [2025_SSDP3A2.kicad_pcb, 2025_SSDP3A2.kicad_sch]
2025-10-06 Changed TVS diode
    [2025_SSDP3A2.kicad_sch]
2025-10-08 Revised input TVS and added input cap
    [2025_SSDP3A2.kicad_pcb, 2025_SSDP3A2.kicad_sch]
2025-10-10 Slightly bigger vout area
    [2025_SSDP3A2.kicad_pcb]
2025-10-11 Improvements to copper, added schematic notations
    [2025_SSDP3A2.kicad_pcb, 2025_SSDP3A2.kicad_sch]
2025-10-11 Improvements to copper, EMI reduction techniques
    [2025_SSDP3A2.kicad_pcb, 2025_SSDP3A2.kicad_sch]
2025-10-11 Updated schematic, added more silkscreen markings
    [2025_SSDP3A2.kicad_pcb, 2025_SSDP3A2.kicad_sch]
2025-10-12 Added more thermal area
    [2025_SSDP3A2.kicad_pcb]
2025-10-13 Added TVS protection to aux IO
    [2025_SSDP3A2.kicad_pcb, 2025_SSDP3A2.kicad_sch]
2025-10-14 Verified compensation network
    [2025_SSDP3A2.kicad_sch]
2025-10-16 Changed parts for LCSC availability, added silkscreen markings
    [2025_SSDP3A2.kicad_pcb, 2025_SSDP3A2.kicad_sch]
2025-10-16 Fixed manufacturing errors
    [2025_SSDP3A2.kicad_pcb, 2025_SSDP3A2.kicad_sch]
2025-10-16 Changed part parameterization
    [2025_SSDP3A2.kicad_pcb, 2025_SSDP3A2.kicad_sch]
2025-10-16 RevC has input polarity protection
    [2025_SSDP3A2.csv, 2025_SSDP3A2.kicad_pcb, 2025_SSDP3A2.kicad_sch]
2025-10-16 Fixed description typo
    [2025_SSDP3A2.kicad_pcb, 2025_SSDP3A2.kicad_sch]
2025-10-17 Fixed BOM typo
    [2025_SSDP3A2.csv, 2025_SSDP3A2.kicad_pcb, 2025_SSDP3A2.kicad_sch]
2025-10-17 Fixed value typo
    [2025_SSDP3A2.csv, 2025_SSDP3A2.kicad_pcb, 2025_SSDP3A2.kicad_sch]
2025-10-17 Added missing thermal vias
    [2025_SSDP3A2.kicad_pcb]
2025-10-17 Repository cleanup
    [2025_SSDP3A2.csv, 2025_SSDP3A2.kicad_pcb, 2025_SSDP3A2.kicad_sch]
2025-10-20 Removed license-restricted files
    [2025_SSDP3A2.kicad_pcb, 2025_SSDP3A2.kicad_sch]
2025-10-20 Officially now the SSDV3
    [SSDV3.csv, SSDV3.kicad_pcb, SSDV3.kicad_sch]
2025-10-20 Fixed paste overlapping soldermask
    [SSDV3.kicad_pcb]
2025-10-22 Minor layout improvements, using original footprints
    [SSDV3.kicad_pcb, SSDV3.kicad_sch]
2025-10-24 Minor layout improvements, improved TSDSON-8 S-D clearance
    [SSDV3.kicad_pcb]
2025-10-24 Improved LM5146 footprint
    [SSDV3.kicad_pcb]
2025-10-31 Added schematic details, added license, improved README
    [SSDV3.kicad_pcb, SSDV3.kicad_sch]
2025-11-03 revD started, fixed reverse polarity issues and improve temp rating
    [SSDV3.csv, SSDV3.kicad_pcb, SSDV3.kicad_sch]
2025-11-03 Updated project documents files
    [SSDV3.kicad_pcb, SSDV3.kicad_sch]
2025-11-05 Refactored schematic into A4 paper, updated PDFs
    [SSDV3.kicad_pcb, SSDV3.kicad_sch, buck_converter.kicad_sch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]
2025-11-09 Layout tweaks, added copyright notice
    [SSDV3.csv, SSDV3.kicad_pcb, SSDV3.kicad_sch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]
